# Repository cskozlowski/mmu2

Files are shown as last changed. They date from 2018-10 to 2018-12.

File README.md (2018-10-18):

DIY Multi Material Upgrade V2.0
==========================
firmware clone project
--------------------------------

This code was developed on an Arduino Mega board using three 8825 stepper motors to control the MMU2 multi-color print head. 
It was designed to operate with the PRUSA mk3 printer.  This code was developed to replace the stock MMU2 controller board, I got bored so I decided to create my own design.  Getting it to play nicely with the mk3 was quite a challenge.  This home brew MMU2 only will operate with the MK3 currently.

You will need an Arduino Mega 2560 processor board and a RAMPS 1.5 or RAMPS 1.6 shield (for the stepper motor controllers) - both are available on Amazon (see my BOM for additional details)

A serial cable is required (5 pin) in order to communicate between this board and the Mk3 controller.  (Vcc, Tx, Rx, GND, Reset).  Only 3 pins are required (Tx, Rx and Reset) in order to work properly with the Mk3.

## WARNING:  
This project is a work in progress and requires a knowledge of Mk3 hardware and software.  If you don't know what you are doing, you can/will PERMANENTLY damage your hardware.  I hope you have been appropriately warned.
          
## ADDITIONAL WARNING
you probably won't read this because it is too far down the page:

**Stepper Motor controllers (8825) are high current devices and they get warm/hot.  You can damage these controller easily
(I have) if you don't adjust the source current.  There is a very small variable resister you will have to adjust, I 
recommend setting this to 0.6V (details on how to adjust this are on the polulu.com website - look for 8825 stepper 
motor controller).  If you don't have a multimeter for measuring voltage then STOP - you are in deep waters.**

# TODOs
* Document Pinouts for each of the stepper motors
* Document Pinouts for 2 sensor cables
* Document Pinouts for Cable between MMU2 controller and MK3 controller (TX, RX, Reset, Vcc)

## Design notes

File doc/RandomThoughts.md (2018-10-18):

Random Thoughts on the DIY MMU 2.0
======================
by Chuck Kozlowski
----------------------------

I started the home-brew MMU2 project on September 19th, 2018.  It has now been 4 weeks and the unit has been working quite well over the past few days after a solid month of tinkering.  Here are a couple of things to help those with their MMU2 adventures not necessarily in any type of useful order:

# 1.  Filament Path
make certain your path from the filament spool all the way to the top of the mk3 extruder is smooth and does not bind.  If there is any binding, find the source (typically at one of the interface points) and fix it.  You will need to do this for each of the 5 filament paths.  I can't emphasize this enough - you need to have each filament path flowing smoothhly in order for the MMU2 to operate correctly.  If you don't do this, you will pay the price for both filament loading and unloading while the MMU2 is attempting to manipulate the filament.

# 2.  Festo Couplers 
I used 10mm OD (threaded) x 4mm (ID) couplers at ALL interface points (one at the selector of the MMU2 and another at the top of the MK3).  My filament touches no metal and this is key to avoid small filament shavings from accumulating while the MMU2 is operating

# 3.  Filament Loading
## Part 1
I realize that the stock MMU2 requires the operator to dial-in the filament length for each of the 5 filaments.  Make certain you take the time to open the bondtech door and see that the filament is going ALL the way to the middle of the bondtech gear. If you don't do this then you will have intermittent filament-load issues which usuallly result in a missing layer during operation
## Part 2
I chose to modify the fundamental design and added a 2nd filament sensor at the top of the MK3 extruder so I know that the filament is actually getting loaded. In fact,  I don't really care about the length of the bowden tube from the MMU2 to the MK3 extruder since the sensor tells me when the filament has arrived.  When the filament arrives,  I push it an additional 31mm and it lands right in the middle of the bondtech gear EVERY time.  I think that the current design of the MMU2 is fundamentally flawed in this area and you will have a difficult time operating 100% of the time without a modification similar to the one I just outlined.

# 4.  Filament Unloading
This is another tricky area since the hot-end does things to the end of the filament during an extraction.  The goal is to form a tip with no stringiness before the filament unload occurs.  If you have not replaced your stock 2.00mm PTFE hot-end part (50mm in length) then STOP reading and go and install the provided part from your kit (1.85mm PTFE).  Since I built my unit from scratch and there is no 1.85mm PTFE in the wild - I procured some 1.80mm PTFE (flurostore.com) and it works wonderfully.  The main reason for this critical piece is to make sure the blob that naturally forms on the end of the filament during a full retraction needs to stay below the magical 2.00mm PTFE ID width.  If you don't do this upgrade then you will have filament unload jamming and that is suck factor 10.

# 5.  Slic3r Settings
Make sure your 'Cooling Moves' are at least 2 when you start.  This is key to forming a properly filament tip during the filament unload process.  Make certain that your 'filament load' setting is at least 21 mm/sec.  I have mine currently set at 30 mm/sec but that is because I have tuned my firmware in the MMU2  to match this speed.  There are some very critical things happending for up to 2 seconds during a filament load when both the MMU2 gears and the MK3 bondtech gear are operating synchronously - if you don't have the speeds match then you will hear filament grinding.  Grinding is not your friend - you will need to adjust the filament load speed until grinding stops.

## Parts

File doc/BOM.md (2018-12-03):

DIY Prusa Multi Material Upgrade (MMU) 2.0
==========================================
Bill of Materials (10.20.2018)
------------------------------
For firmware, please refer to https://github.com/cskozlowski/mmu2

Be warned, this is a very difficult project. 
Everyone wants to know the $$$, the list below is under $200 (US). 
The most expensive parts are:  stepper motors ($30 for the three I purchased), arduino ($14) and RAMPS 1.6 board ($14).
This is a starter list of stuff you will need to complete this MMU2 home brew clone

# Change Notes:
* 10.20.18 Added another stepper motor alternative (w/ proper axles) - from aliexpress.com
* 10.17.18 Added 3 STL files required for build of the home-brew MMU2 (do the NEMA17 holder in PETG, other pieces can be 
                                                                          done in PLA or PETG)
* 10.16.18 Changed the stepper motor recommendation, you can also get them on aliexpress.com)
* 10.10.18  Added references to 3 STL design files that you will need (see STL for additional details)
* 10.9.18   626-ZZ should say 625-ZZ bearings ... 626-ZZ are rarer than 1.85mm PTFE
* 10.9.18   Added 7mm ball bearing (you need this for the FINDA detector)
* 10.9.18   Added 5mm x 8mm coupler (need this for the selector stepper motor to threaded rod)

# BOM

## Prusa Parts
* MMU2 plastic parts - https://www.prusa3d.com/prusa-i3-printable-parts/

## Motors

* ~~3 Stepper Motors~~
  (DO NOT PURCHASE THESE MOTORS, THEY DO NOT HAVE SUFFICIENT STALL TORQUE)(https://www.amazon.com/gp/product/B0716S32G4/ref=oh_aui_detailpage_o03_s00?ie=UTF8&psc=1)
            (these motors are super cheap $10 per motor ... don't buy them because they don't have sufficient torque)
            (I used them for 3 weeks and chased problems that won't be there if you get better motors
            (get the motors I list below)

* 3   Stepper Motors 
  (PURCHASE THESE STEPPER MOTORS INSTEAD)(https://www.amazon.com/gp/product/B06XSYP24P/ref=oh_aui_detailpage_o01_s00?ie=UTF8&psc=1)

  (these motors have 46 N-cm of stall torque.  They idler stepper motor needs quite a bit of stall torque to stay
            in place when the bearing is being moved against the extruder stepper motor).
            
  Get a motor with a minimum of 45 N-cm of stall torque (you will thank me later)
         
  Another potential alternative is these 3 stepper motors (they have proper shafts for the MMU2)
   https://www.aliexpress.com/item/Prusa-i3-mk3-mk2-5-Multi-materials-2-0-3d-printer-motor-kit-MMU2-0/32923672790.html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   (I have them on order but have not received them yet for testing)

## Other Stuff
* 5   mk8 hobbed gears (https://www.amazon.com/gp/product/B07CJPP7R7/ref=oh_aui_detailpage_o03_s00?ie=UTF8&psc=1)
* 2   100mm x 5mm steel shafts (https://www.amazon.com/gp/product/B01B27MJC6/ref=oh_aui_detailpage_o04_s00?ie=UTF8&psc=1)
     (these shafts are used to make your 16mm spindles for the bearings,  you can also order 16mm x 5mm spindles from McMcaster-Carr,
     (however, they are wicked tight on the bearings)
* 2   150mm x 5mm steel shafts (https://www.amazon.com/gp/product/B01B5QTM8I/ref=oh_aui_detailpage_o01_s00?ie=UTF8&psc=1)
      (these shafts are used for the selector head shaft guides, you will have to cut them down to size)
      (if you don't know how to cut steel shafts then please stop and go do something else)
* 9   625-ZZ bearings (https://www.amazon.com/gp/product/B01CUTIQWW/ref=oh_aui_detailpage_o04_s01?ie=UTF8&psc=1)
* 20  3mm thin (1.8mm) square nuts) https://www.amazon.com/gp/product/B073SBCMBM/ref=oh_aui_detailpage_o05_s00?ie=UTF8&psc=1
* 1   5mm x 5mm coupler https://www.amazon.com/gp/product/B0159WO7T8/ref=oh_aui_detailpage_o02_s00?ie=UTF8&psc=1
                     (you need one but buy two because you can) 
* 1   5mm x 8mm coupler  (amazon.com ... too lazy to provide the link at the moment).
* 25' 4mm OD x 2mm ID PTFE Tubing (https://www.amazon.com/gp/product/B073RFQQ3Z/ref=oh_aui_detailpage_o09_s00?ie=UTF8&th=1)
                     Needed for the feeders from the spools to the MMU2 unit, you will learn to hate PTFE tubing
* 1   50mm 4mm OD x 1.85mm ID PTFE Tubing (flurostore.com has 1.80mm ID tubing - it works !!!)
                By far the most difficult part to obtain, it should just be called unobtanium
* 1   150mm x 8mm threaded shaft (https://www.amazon.com/gp/product/B07C8P1DWX/ref=oh_aui_detailpage_o08_s01?ie=UTF8&psc=1)
                (yes, you will have to cut it to size using some of your cool shop tools)
* 10  PC4-10 PTFE connectors (https://www.amazon.com/gp/product/B01IB81IHG/ref=oh_aui_detailpage_o02_s00?ie=UTF8&psc=1)
                (get these, they are awesome)
* 1   12-15V, 2A  Power supply - needed for the Arduino Mega/RAMPS board for initial testing
* 1   Arduino Mega 2560 (https://www.amazon.com/gp/product/B01H4ZDYCE/ref=oh_aui_detailpage_o01_s00?ie=UTF8&psc=1)
* 1   1.x RAMPS Boards (https://www.amazon.com/gp/product/B0794YN8XK/ref=oh_aui_detailpage_o09_s00?ie=UTF8&psc=1)
                    (home for all of your stepper motor controllers)
* 3  8825 Stepper Motor Controller (https://www.amazon.com/gp/product/B00S3Q9YZA/ref=oh_aui_detailpage_o05_s00?ie=UTF8&psc=1)
                    (make certain to tweak the voltage rheostat on the top of this little wonder, goto polulu website)
                    (I currently have mine set to 0.60V - don't go too high you will fry this component)
* 1  Razor Blades (https://www.amazon.com/gp/product/B007QYAJRC/ref=oh_aui_detailpage_o07_s00?ie=UTF8&psc=1)
* 1  microswitch   (https://www.amazon.com/gp/product/B06XSBYQ8H/ref=oh_aui_detailpage_o05_s00?ie=UTF8&psc=1)
* 1  FINDA (aka PINDA) Probe (https://www.amazon.com/URBEST-Detecting-Distance-Inductive-Proximity/dp/B01M1777XK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)
                  ( I had a spare probe laying around so I have NOT tried this inductive probe)
                  (they are also available from aliexpress.com)
* 1  7mm ball bearing  (mcmaster.carr or amazon), you only need one but you will have to buy many more
* 2  6mm OD x .45mm thick brass tubing (ksmetals.com - part #982, this comes in 300mm length and you will have to cut it down)

## Custom STL Files
* 1  MMU2 to PTFE Festo Coupler 
* 1  MK3 to PTFE Festo Coupler (w/ microswitch holder)
* 1  Selector Motor Mount offset block

## DigiKey Components (needed for cables and wiring)
(to be completed)

## Random Tools
(it's a project, you've got to buy new tools - you live for this stuff)
* 1 Reamer (https://www.amazon.com/gp/product/B01EIH573K/ref=oh_aui_detailpage_o07_s00?ie=UTF8&psc=1)
           (used to make awesome interior bevelled edges in that damn 2mm (and 1.80mm) PTFE
* 50mm cutting jig (https://www.thingiverse.com/thing:3062809)    
           (oh look, you get to make something with your 3d printer)

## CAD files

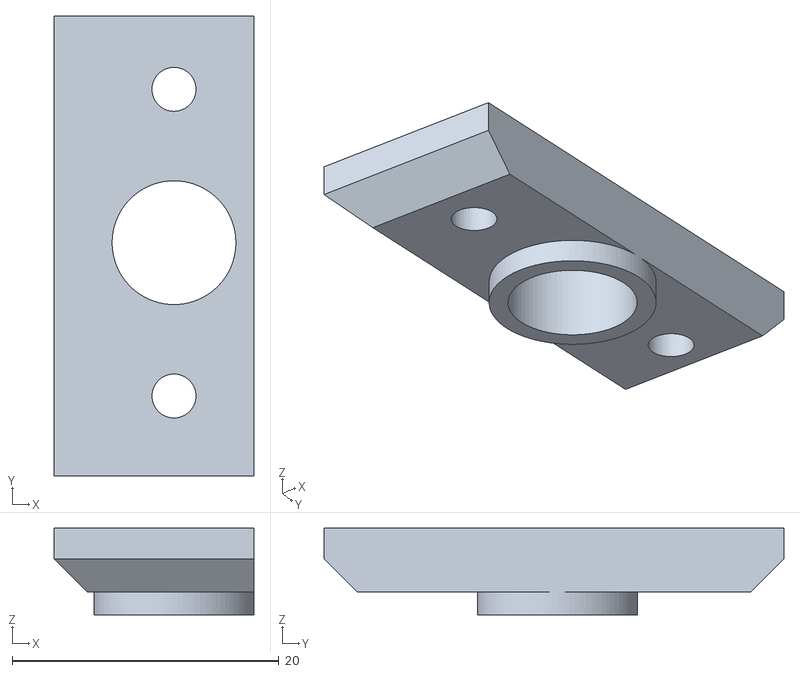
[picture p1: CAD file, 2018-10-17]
stls/MMU2 Selector Cover with modified center hole.stl
15.0 x 34.5 x 6.50

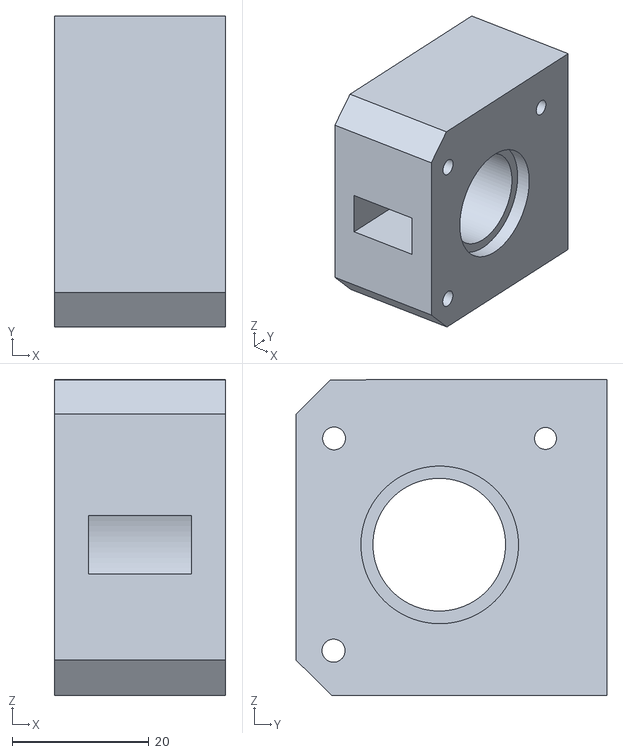
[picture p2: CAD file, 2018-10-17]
stls/NEMA17 Motor Holder Offset for MMU2.stl
25.0 x 45.4 x 46.2

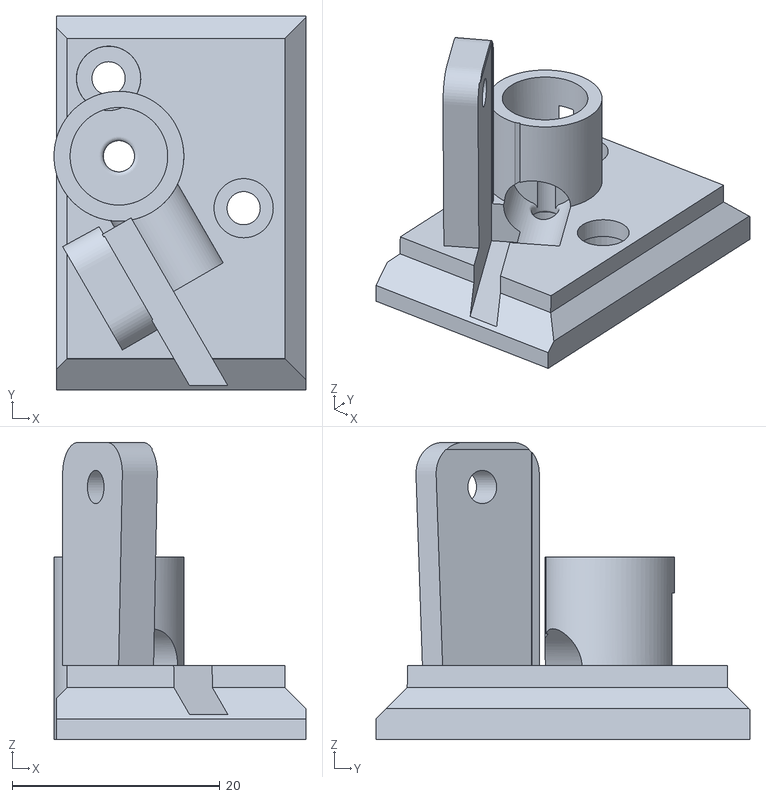
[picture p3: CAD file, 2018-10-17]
stls/MK3 Filament Cover (CSK Design).stl
24.3 x 36.0 x 28.6

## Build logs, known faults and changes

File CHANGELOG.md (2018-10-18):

Changelog for DIY MMU 2.0
=========================

# 2018-10-18
* refactored repository
* restructured folders and filenames
* add platformio.ini
* add wrapper class Application for compatibility with
  Arduino IDE and Platformio with QtCreator.
  Tested compiling with Arduino IDE 1.8.5
* reduced RAM usage using progmem macro F() from 139% to 45%
  for Arduino Leonardo

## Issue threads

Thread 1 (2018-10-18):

BOM as markdown

KarlZeilhofer, 2018-10-18:
Dear Chuk,

I've reformatted your BOM, to be a markdown file and added the link to this github repo:

Here is the code:
```
DIY Prusa Multi Material Upgrade (MMU) 2.0
==========================================
Bill of Materials (10.7.2018)
------------------------------
For firmware, please refer to https://github.com/cskozlowski/mmu2

Be warned, this is a very difficult project.
Everyone wants to know the $$$, the list below is under $200 (US).
The most expensive parts are:  stepper motors ($30 for the three I purchased), arduino ($14) and RAMPS 1.6 board ($14).
This is a starter list of stuff you will need to complete this MMU2 home brew clone

# Change Notes:
* 10.17.18 Added 3 STL files required for build of the home-brew MMU2 (do the NEMA17 holder in PETG, other pieces can be
                                                                          done in PLA or PETG)
* 10.16.18 Changed the stepper motor recommendation, you can also get them on aliexpress.com)
* 10.10.18  Added references to 3 STL design files that you will need (see STL for additional details)
* 10.9.18   626-ZZ should say 625-ZZ bearings ... 626-ZZ are rarer than 1.85mm PTFE
* 10.9.18   Added 7mm ball bearing (you need this for the FINDA detector)
* 10.9.18   Added 5mm x 8mm coupler (need this for the selector stepper motor to threaded rod)

# BOM

## Prusa Parts
* MMU2 plastic parts - https://www.prusa3d.com/prusa-i3-printable-parts/

## Motors

* 3 Stepper Motors
  (DO NOT PURCHASE THESE MOTORS, THEY DO NOT HAVE SUFFICIENT STALL TORQUE)(https://www.amazon.com/gp/product/B0716S32G4/ref=oh_aui_detailpage_o03_s00?ie=UTF8&psc=1)
            (these motors are super cheap $10 per motor ... don't buy them because they don't have sufficient torque)
            (I used them for 3 weeks and chased problems that won't be there if you get better motors
            (get the motors I list below)

* 3   Stepper Motors
  (PURCHASE THESE STEPPER MOTORS INSTEAD)(https://www.amazon.com/gp/product/B06XSYP24P/ref=oh_aui_detailpage_o01_s00?ie=UTF8&psc=1)

  (these motors have 46 N-cm of stall torque.  They idler stepper motor needs quite a bit of stall torque to stay
            in place when the bearing is being moved against the extruder stepper motor).
    
  Get a motor with a minimum of 45 N-cm of stall torque (you will thank me later)
 
    These motors are nice and cheap - the problem with cheap is they are not 100% reliable. I am testing another brand at the
    moment and when I have some decent test results I will report back.

## Other Stuff
* 5   mk8 hobbed gears (https://www.amazon.com/gp/product/B07CJPP7R7/ref=oh_aui_detailpage_o03_s00?ie=UTF8&psc=1)
* 2   100mm x 5mm steel shafts (https://www.amazon.com/gp/product/B01B27MJC6/ref=oh_aui_detailpage_o04_s00?ie=UTF8&psc=1)
     (these shafts are used to make your 16mm spindles for the bearings,  you can also order 16mm x 5mm spindles from McMcaster-Carr,
     (however, they are wicked tight on the bearings)
* 2   150mm x 5mm steel shafts (https://www.amazon.com/gp/product/B01B5QTM8I/ref=oh_aui_detailpage_o01_s00?ie=UTF8&psc=1)
      (these shafts are used for the selector head shaft guides, you will have to cut them down to size)
      (if you don't know how to cut steel shafts then please stop and go do something else)
* 9   625-ZZ bearings (https://www.amazon.com/gp/product/B01CUTIQWW/ref=oh_aui_detailpage_o04_s01?ie=UTF8&psc=1)
* 20  3mm thin (1.8mm) square nuts) https://www.amazon.com/gp/product/B073SBCMBM/ref=oh_aui_detailpage_o05_s00?ie=UTF8&psc=1
* 1   5mm x 5mm coupler https://www.amazon.com/gp/product/B0159WO7T8/ref=oh_aui_detailpage_o02_s00?ie=UTF8&psc=1
                     (you need one but buy two because you can)
* 1   5mm x 8mm coupler  (amazon.com ... too lazy to provide the link at the moment).
* 25' 4mm OD x 2mm ID PTFE Tubing (https://www.amazon.com/gp/product/B073RFQQ3Z/ref=oh_aui_detailpage_o09_s00?ie=UTF8&th=1)
                     Needed for the feeders from the spools to the MMU2 unit, you will learn to hate PTFE tubing
* 1   50mm 4mm OD x 1.85mm ID PTFE Tubing (flurostore.com has 1.80mm ID tubing - it works !!!)
                By far the most difficult part to obtain, it should just be called unobtanium
* 1   150mm x 8mm threaded shaft (https://www.amazon.com/gp/product/B07C8P1DWX/ref=oh_aui_detailpage_o08_s01?ie=UTF8&psc=1)
                (yes, you will have to cut it to size using some of your cool shop tools)
* 10  PC4-10 PTFE connectors (https://www.amazon.com/gp/product/B01IB81IHG/ref=oh_aui_detailpage_o02_s00?ie=UTF8&psc=1)
                (get these, they are awesome)
* 1   12-15V, 2A  Power supply - needed for the Arduino Mega/RAMPS board for initial testing
* 1   Arduino Mega 2560 (https://www.amazon.com/gp/product/B01H4ZDYCE/ref=oh_aui_detailpage_o01_s00?ie=UTF8&psc=1)
* 1   1.x RAMPS Boards (https://www.amazon.com/gp/product/B0794YN8XK/ref=oh_aui_detailpage_o09_s00?ie=UTF8&psc=1)
                    (home for all of your stepper motor controllers)
* 3  8825 Stepper Motor Controller (https://www.amazon.com/gp/product/B00S3Q9YZA/ref=oh_aui_detailpage_o05_s00?ie=UTF8&psc=1)
                    (make certain to tweak the voltage rheostat on the top of this little wonder, goto polulu website)
                    (I currently have mine set to 0.60V - don't go too high you will fry this component)
* 1  Razor Blades (https://www.amazon.com/gp/product/B007QYAJRC/ref=oh_aui_detailpage_o07_s00?ie=UTF8&psc=1)
* 1  microswitch   (https://www.amazon.com/gp/product/B06XSBYQ8H/ref=oh_aui_detailpage_o05_s00?ie=UTF8&psc=1)
* 1  FINDA (aka PINDA) Probe (https://www.amazon.com/URBEST-Detecting-Distance-Inductive-Proximity/dp/B01M1777XK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)
                  ( I had a spare probe laying around so I have NOT tried this inductive probe)
                  (they are also available from aliexpress.com)
* 1  7mm ball bearing  (mcmaster.carr or amazon), you only need one but you will have to buy many more

## Custom STL Files
* 1  MMU2 to PTFE Festo Coupler
* 1  MK3 to PTFE Festo Coupler (w/ microswitch holder)
* 1  Selector Motor Mount offset block

## DigiKey Components (needed for cables and wiring)
(to be completed)

## Random Tools
(it's a project, you've got to buy new tools - you live for this stuff)
* 1 Reamer (https://www.amazon.com/gp/product/B01EIH573K/ref=oh_aui_detailpage_o07_s00?ie=UTF8&psc=1)
           (used to make awesome interior bevelled edges in that damn 2mm (and 1.80mm) PTFE
* 50mm cutting jig (https://www.thingiverse.com/thing:3062809)
           (oh look, you get to make something with your 3d printer)
   
```

And here how it would be rendered in github:
----

DIY Prusa Multi Material Upgrade (MMU) 2.0
==========================================
Bill of Materials (10.7.2018)
------------------------------
For firmware, please refer to https://github.com/cskozlowski/mmu2

Be warned, this is a very difficult project.
Everyone wants to know the $$$, the list below is under $200 (US).
The most expensive parts are:  stepper motors ($30 for the three I purchased), arduino ($14) and RAMPS 1.6 board ($14).
This is a starter list of stuff you will need to complete this MMU2 home brew clone

# Change Notes:
* 10.17.18 Added 3 STL files required for build of the home-brew MMU2 (do the NEMA17 holder in PETG, other pieces can be
                                                                          done in PLA or PETG)
* 10.16.18 Changed the stepper motor recommendation, you can also get them on aliexpress.com)
* 10.10.18  Added references to 3 STL design files that you will need (see STL for additional details)
* 10.9.18   626-ZZ should say 625-ZZ bearings ... 626-ZZ are rarer than 1.85mm PTFE
* 10.9.18   Added 7mm ball bearing (you need this for the FINDA detector)
* 10.9.18   Added 5mm x 8mm coupler (need this for the selector stepper motor to threaded rod)

# BOM

## Prusa Parts
* MMU2 plastic parts - https://www.prusa3d.com/prusa-i3-printable-parts/

## Motors

* 3 Stepper Motors
  (DO NOT PURCHASE THESE MOTORS, THEY DO NOT HAVE SUFFICIENT STALL TORQUE)(https://www.amazon.com/gp/product/B0716S32G4/ref=oh_aui_detailpage_o03_s00?ie=UTF8&psc=1)
            (these motors are super cheap $10 per motor ... don't buy them because they don't have sufficient torque)
            (I used them for 3 weeks and chased problems that won't be there if you get better motors
            (get the motors I list below)

* 3   Stepper Motors
  (PURCHASE THESE STEPPER MOTORS INSTEAD)(https://www.amazon.com/gp/product/B06XSYP24P/ref=oh_aui_detailpage_o01_s00?ie=UTF8&psc=1)

  (these motors have 46 N-cm of stall torque.  They idler stepper motor needs quite a bit of stall torque to stay
            in place when the bearing is being moved against the extruder stepper motor).
    
  Get a motor with a minimum of 45 N-cm of stall torque (you will thank me later)
 
    These motors are nice and cheap - the problem with cheap is they are not 100% reliable. I am testing another brand at the
    moment and when I have some decent test results I will report back.
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
KarlZeilhofer, 2018-10-18:
Keep up your great work!
Greets, Karl

KarlZeilhofer, 2018-10-18:
PS: main purpose was to get clickable links for the lazy human :)

martinj, 2018-10-18:
@KarlZeilhofer maybe do a Pull Request for this?

knoopx, 2018-10-18:
Click here: https://github.com/cskozlowski/mmu2/edit/master/README.md and paste the new readme :)

KarlZeilhofer, 2018-10-18:
I didn't want to confuse him with a pullrequest.

PPS: Until now I used Marp as a Markdown editor. But now I found Ghostwirter: This tool is awesome: https://wereturtle.github.io/ghostwriter/

If you are familiar with German, you can find some thoughts from me here: http://www.zeilhofer.co.at/wiki/doku.php?id=markdown#ghostwriter

KarlZeilhofer, 2018-10-18:
@knoopx beware that I posted about the BOM, not the README.md

KarlZeilhofer, 2018-10-18:
ok, i did a pullrequest now to bring this repo in a "standard" Github format: #2

Closed 2018-10-18.

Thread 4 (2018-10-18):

gcc warning about integer overflow

KarlZeilhofer, 2018-10-18:
The line `		steps = 17 * 200 * STEPSIZE; `` in ``void loadFilament(int direction)`` results in about 54k, which gives an signed integer overflow.

Adding ``ul`` specifiers (for unsigned long) fixes this issue.

cskozlowski, 2018-10-18:
This was how I originally moved the filament past the PINDA sensor to get to the bondtech gear.

I no longer use this method since I have the 2nd sensor - you will see in the code that I move the filament 350 mm (way before 2nd sensor) and then go into a 'sensor loop' to wait for the filament to show up and then move it an addition 31mm (if I remember correctly) so it gets right to the middle of the bondtech gear.  I now make all filament moves in mm moves (144*# of mm).

KarlZeilhofer, 2018-10-18:
same for
``	feedFilament(STEPSPERMM * 350);       // go 350 mm then look for the 2nd filament sensor``
in
``void filamentLoadToMK3()``

fixed it by defining `STEPSPERMM` as `unsigned long`

cskozlowski, 2018-10-18:
The call for 17 * 200 * STEPSIZE (part of loadfilament() routine) is not called operationally.

The feedFilament call (STEPSPERMM *350)  is below 65,535 so and unsigned int should be sufficient since I only need 16 bits for that value.

cskozlowski, 2018-10-18:
I can say that this call - the filamentLoadtoMK3() works since it a core part of my operational code and I have had no issues with unsigned int.  Changing it to unsigned long is not bad though because then I can make the bowden tube (between the MMU2 and the MK3) longer and not worry if I go past 65,535.

cskozlowski, 2018-10-18:
Since you are using the leonardi board and the existing trinamic drivers.  Be aware that I am using steps sizes on my 8255 set to 16 (you can see that at the top of my code).  I do not know the step setup of the current trinamic drivers (it is probably either 16 or 32 so they run quieter).

KarlZeilhofer, 2018-10-18:
thanks for that hint, I have to rewrite the drivers setup anyway. I will stick to your config where possible.

Prusa has configured them to halfstep (selector and pulley) and 16th step (idler)

cskozlowski, 2018-10-18:
Thats good to know the production stepper rates, if I move to halfstep then I can really speed up both the extruder and selector stepper motors on my setup.  I played with the stepper motor speeds but dialed them back so that it worked 100% of the time.  My delay values for the stepper motors are at the top of the code and I messed with them quite a bit to get them dialed in correctly.

cskozlowski, 2018-10-18:
I am excited about your port of this code base to the leonardo board.  Are you going to tack on a sensor to make full use of my code or do something different?

cskozlowski, 2018-10-18:
The stepper motor driver rewrite shouldn't be too difficult.  I now have some trinamic stepper motor controllers in my possession so I need to  try and get those up and running as well (too many projects).

KarlZeilhofer, 2018-10-18:
Of course I want to use your mod with the micro switch above the extruder. That's the whole idea - and to show, that Prusa can keep their code for their own. Nobody needs such a piece of crap combined with their pride. They haven't even answered my quotation eMail within 3 days.

What is missing in your motion controll (same was the case at Prusa's code) are acceleration phases. I wrote some nice code, which does that. That's why the selector in my video can go that fast.

KarlZeilhofer, 2018-10-18:
May I ask what your time zone is?

KarlZeilhofer, 2018-10-18:
email is fine for me. zeilhofer a   t   team14    d-o-t    at

KarlZeilhofer, 2018-10-18:
have you sent an eMail?

cskozlowski, 2018-10-18:
yep ... checking the address

jettoblack, 2018-10-19:
I don't have my hardware yet but I am following this FW development with much interest! I'm still thinking of making a selector-less version that uses a 5 filament combiner instead.

bula87, 2018-11-08:
Also joining the party. Today I get my Ramps. Now I just need to print everything and assembly it :D

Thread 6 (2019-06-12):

europe sources

boelle, 2019-06-12:
any that has europe sources?

spec the brass tubes and steel shafts (both the short and long ones)

china sources are ok'ish, but it takes a month or more to get here and the price is for a complete kit is just above the free limit where i dont have to pay import fees

so anything inside the EU would be much more ideal

cskozlowski, 2019-06-12:
I am not versed in EU manufacturing sources.

boelle, 2019-06-12:
it was more like a shout out to anyone that see it :-)

hope its ok

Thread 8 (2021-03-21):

Stepper drivers - SPI or UART?

ss32, 2021-03-21:
I'd like to use the [TMC2130](https://www.trinamic.com/products/integrated-circuits/details/tmc2130/) drivers since they're quieter than standard drivers, but they're offered in both SPI and UART configurations and I was wondering what protocol this project uses.

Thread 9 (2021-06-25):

No communication between printer and MMU

wikolii, 2021-06-25:
Hi, 1st of all thanks for the code,. I love the project and being able to make your own MMU is so cool.

I have the MMU firmware uploaded to an SKR mini e3 v2. Everything seems to work because it starts and homes the idler.
The printer has an SKR v1.4 pro board, and it's able to reset the MMU, even respond after the MMU starts but then it just sits there and doesn't respond to any commands from the printer's LCD MMU menu.

Here's the serial output:

18:37:29.848 -> waiting for serial port
18:37:29.848 -> 6.0 16/12/21
18:37:29.848 -> Sending START command to mk3 controller board
18:37:29.848 -> Sending START command to mk3 controller board
18:37:29.848 -> Starting new beta v 1.0
18:37:29.848 -> Waiting for message from mk3
18:37:29.848 -> Sending START command to mk3 controller board
18:37:29.848 -> Starting new beta v 1.0
18:37:29.848 -> Waiting for message from mk3
18:37:30.875 -> inbound message from Marlin
18:37:30.875 -> finished setting up input and output pins
18:37:31.015 -> Syncing the Idler Selector Assembly
18:37:32.278 -> Idler homed
18:37:33.493 -> Inialialization Complete, let's multicolor print ....
18:37:33.586 -> MMU Command: 'echo:Unknown command: "atr"'
18:37:33.586 -> ERROR: unrecognized command from the MK3 controllerMMU Command: 'ok'
18:37:33.680 -> ERROR: unrecognized command from the MK3 controllerMMU Command: 'echo:Unknown command: "o"'
18:37:33.773 -> ERROR: unrecognized command from the MK3 controllerMMU Command: 'ok'

and so on...

Any ideas? what's that "atr" command? Maybe i need to set a different MMU_RX / TX_SIZE?

I'd appreciate any kind of help, thanks in advance!

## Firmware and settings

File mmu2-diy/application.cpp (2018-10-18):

// CSK MMU2 Controller Version
//
//  Code developed by Chuck Kozlowski
//  September 19, 2018
//
//  Code was developed because I am impatiently waiting for my MMU2 to arrive (due in December, 2018) so I thought
//  I would develop some code to operate the PRUSA MMU2 hardware
//
// This code uses 3 stepper motor controllers and 1 Pinda filament sensor, and 1 additional filament sensor on the mk3 extruder top
//
//
//  Work to be done:  Interface Control with the Einsy Board (MK3) - (work completed on 9.25.18)
//                    Refine speed and acceleration settings for each stepper motor
//                    Failure Recovery Modes - basically non-existent (work completed on 10.5.18)
//
//                    Uses the serial interface with a host computer at the moment - probably could do some smarter things
//                                                                                   like selection switches and some LEDs.
//                   10.14.18 Leave the Selector Stepper Motor ON ... appear to be losing position with the selector during operation
//                            [now using the J-4218HB2301 Stepper Motor - (45 N-cm torque) as the idler stepper motor]
//                   10.14.18 Added yet another idler command set (specialparkidler() and specialunparkidler) - used within the 'C' Command
//                            Idler management is a bit of challenge,  probably has more to do with my coding skills (or lack thereof).
//                   10.12.18 Minor fix to idler parking ... now use quickparkidler() after 'C' command and quickunparkidler() at beginning of 'T' command
//                              This helps to speed up the idler movements during 'T' and 'C' commands
//                   10.5.18  Made major tweak to the 'C' command, now matches the speed of the mk3 extruder gear (see slic3r 'load' setting)
//                   10.2.18  Moved from breadboard to RAMPS 1.6 Board and remapped ALL addresses
//                            Discovered the filament idler motor needed to be set at a higher torque (more current)
//                            (this was affected filament load consistency)
//                   10.2.18  Major Disaster, lost my codebase on my PC (I am an idiot)
//                            Thank God for github so I could recover a week old version of my code
//                   10.1.18  Added filament sensor to the extruder head (helps reliability


//#include <SoftwareSerial.h>
#include <Arduino.h>
#include <stdio.h>
#include <string.h>
#include <stdarg.h>
#include "application.h"



static int isFilamentLoaded();
static void initIdlerPosition();
static void checkSerialInterface();
static void initColorSelector();
static void filamentLoadWithBondTechGear();
static void toolChange( char selection);
static void quickUnParkIdler();
static void unParkIdler();
static void unloadFilamentToFinda();
static void parkIdler();
static void activateColorSelector();
static void idlerSelector(char filament);
static void colorSelector(char selection);
static void loadFilamentToFinda();
static void fixTheProblem(String statement);
static void csTurnAmount(int steps, int direction);
static void feedFilament(unsigned int steps);


#define SERIAL1ENABLED    1
#define ENABLE LOW                // 8825 stepper motor enable is active low
#define DISABLE HIGH              // 8825 stepper motor disable is active high

#define MMU2_VERSION "4.2  10/12/18"

#define STEPSPERMM  144           // these are the number of steps required to travel 1 mm using the extruder motor

#define FW_VERSION 90             // config.h  (MM-control-01 firmware)
#define FW_BUILDNR 85             // config.h  (MM-control-01 firmware)

#define ORIGINALCODE 0            // code that is no longer needed for operational use
int command = 0;

// changed from 125 to 115 (10.13.18)
#define MAXROLLERTRAVEL 125         // number of steps that the roller bearing stepper motor can travel

#define FULL_STEP  1
#define HALF_STEP  2
#define QUARTER_STEP 4
#define EIGTH_STEP 8
#define SIXTEENTH_STEP 16

#define STEPSIZE SIXTEENTH_STEP    // setup for each of the three stepper motors (jumper settings for M0,M1,M2) on the RAMPS 1.x board

#define STEPSPERREVOLUTION 200     // 200 steps per revolution  - 1.8 degree motors are being used

#define MAXSELECTOR_STEPS   1890   // maximum number of selector stepper motor (used to move all the way to the right or left

#define MMU2TOEXTRUDERSTEPS STEPSIZE*STEPSPERREVOLUTION*19   // for the 'T' command 

#define CW 0
#define CCW 1

#define INACTIVE 0                           // used for 3 states of the idler stepper motor (parked)
#define ACTIVE 1                             // not parked 
#define QUICKPARKED 2                            // quick parked


//************************************************************************************
//* this resets the selector stepper motor after the selected number of tool changes
//* changed from 25 to 10 (10.10.18)
//* chagned from 10 to 8 (10.14.18)
//*************************************************************************************
#define TOOLSYNC 20                         // number of tool change (T) commands before a selector resync is performed



#define PINHIGH 10                    // how long to hold stepper motor pin high in microseconds
#define PINLOW  10                    // how long to hold stepper motor pin low in microseconds



// the MMU2 currently runs at 21mm/sec (set by Slic3r) for 2 seconds (good stuff to know)
//
// the load duration was chagned from 1 second to 1.1 seconds on 10.8.18 (as an experiment)
// increased from 1.1 to 1.5 seconds on 10.13.18 (another experiment)
#define LOAD_DURATION 1600                 // duration of 'C' command during the load process (in milliseconds)


// changed from 21 mm/sec to 30 mm/sec on 10.13.18
#define LOAD_SPEED 30                   // load speed (in mm/second) during the 'C' command (determined by Slic3r setting)
#define INSTRUCTION_DELAY 25          // delay (in microseconds) of the loop



#define IDLERSTEPSIZE 23         // steps to each roller bearing  
//float bearingAbsPos[5] = {1, 24, 48, 72, 96}; // absolute position of roller bearing stepper motor
float bearingAbsPos[5] = {0, IDLERSTEPSIZE, IDLERSTEPSIZE * 2, IDLERSTEPSIZE * 3, IDLERSTEPSIZE * 4};



// changed position #2 to 372  (still tuning this little sucker)


#define CSSTEPS 357                        //                                                 
int selectorAbsPos[5] = {0, CSSTEPS * 1, CSSTEPS * 2, CSSTEPS * 3, CSSTEPS * 4}; // absolute position of selector stepper motor


int trackToolChanges = 0;
int extruderMotorStatus = INACTIVE;


int currentCSPosition = 0;         // color selector position
int currentPosition = 0;

int repeatTCmdFlag = INACTIVE;    // used by the 'C' command processor to avoid processing multiple 'C' commands
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

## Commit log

2018-09-25 Add files via upload
    This is my original source code for the arduino Mega with 8255 stepper motors.
2018-10-03 Added new version of the mmu2 home brew controller
    This code adds a key new element (filament switch at the mk3 extruder). Makes for better filament loads
2018-10-03 Add files via upload
    Minor additional tweaks to the code. I managed to destroy 2 Arduino Mega controller boards (destroyed UARTS). 2 new boards on order.
2018-10-06 Add files via upload
    Tweaks to loading of filament to match the mk3 extruder ....
2018-10-07 Create BOM (Initial)
    Parts List for the Home Brew MMU2
2018-10-07 Update BOM (Initial)
    added FINDA probe.
2018-10-07 Update BOM (Initial)
2018-10-08 Add files via upload
    The idler pulley was getting moved way too much. Rewrote the idler movements between the 'T' command and 'C' command (these come from the MMU2) and voila .. much more effecient idler movements are now happening.
2018-10-09 Add files via upload
    Made minor changes to filament load/unload error conditions
2018-10-17 Add files via upload
    STL files of custom designed parts required for the home-brew MMU2
    [MK3 Filament Cover (CSK Design).stl, NEMA17 Motor Holder Offset for MMU2.stl]
2018-10-18 put files into folders, version V0.0
    [MK3 Filament Cover (CSK Design).stl, MMU2 Selector Cover with modified center hole.stl, NEMA17 Motor Holder Offset for MMU2.stl]
2018-10-18 add platformio ini for Prusas MMU controller board
2018-10-18 setup platformio and tested arduino compatibility
2018-10-18 bugfix in compatibility layer, compiles now in Arduino IDE and Platformio!
    [application.cpp]
2018-10-18 reduced RAM usage from 140% to 72% by using some F() macros, ...
    please refer to http://www.zeilhofer.co.at/wiki/doku.php?id=regex#arduino_and_progmem
